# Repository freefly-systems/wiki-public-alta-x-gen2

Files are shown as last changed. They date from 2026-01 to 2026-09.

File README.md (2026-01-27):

# Alta X Gen2

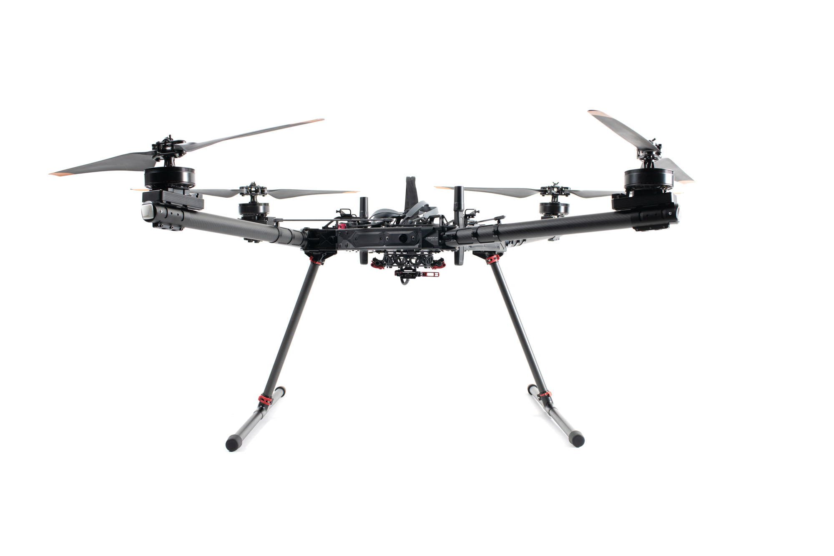
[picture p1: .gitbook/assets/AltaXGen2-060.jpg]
<figure><figcaption></figcaption></figure>

Alta X Gen2 is a professional multi-rotor aircraft designed for demanding cinematic, professional, and industrial applications. Building on the proven foundation of the original Alta X and incorporating advanced technologies from Astro, Gen2 delivers significant performance improvements alongside enhanced intelligence and capability. Alta X Gen2 continues the Freefly tradition of expandability and customization while bringing new innovations to the reliable workhorse platform that Alta pilots trust for their most critical missions.

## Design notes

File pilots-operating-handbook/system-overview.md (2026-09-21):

---
icon: book-open-lines
---

# System Overview

<figure><figcaption></figcaption></figure>

Alta X Gen2 is a professional multi-rotor aircraft designed for demanding cinematic, professional, and industrial applications. Building on the proven foundation of the original Alta X and incorporating advanced technologies from Astro, Gen2 delivers significant performance improvements alongside enhanced intelligence and capability. Alta X Gen2 continues the Freefly tradition of expandability and customization while bringing new innovations to the reliable workhorse platform that Alta pilots trust for their most critical missions.

## Key Components

### Alta X Gen2

Alta X Gen2 comes standard with 12mm rails and the Smart Dovetail isolator for quick payload swaps.

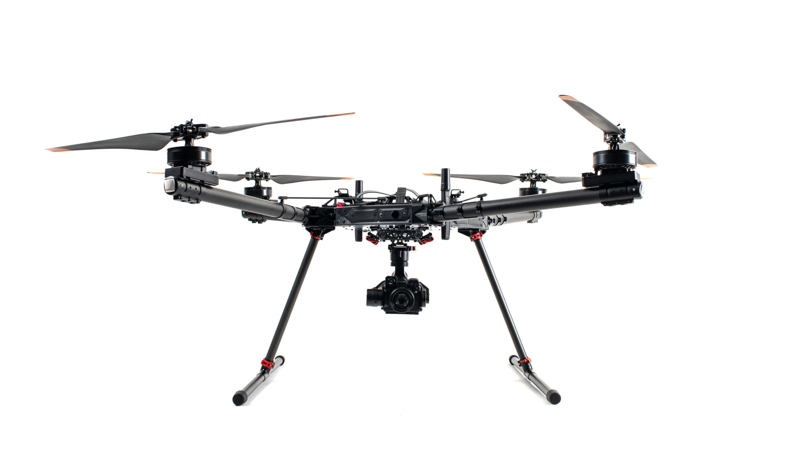
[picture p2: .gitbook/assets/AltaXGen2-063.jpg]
<figure><figcaption></figcaption></figure>

### Pilot Pro

Alta X Gen2 ships with [Pilot Pro](https://freeflysystems.com/pilot-pro), our custom controller, with either Herelink or Doodle radio. For more information, check the [Pilot Pro wiki](https://docs.freeflysystems.com/ecosystem/controller/pilot-pro/).

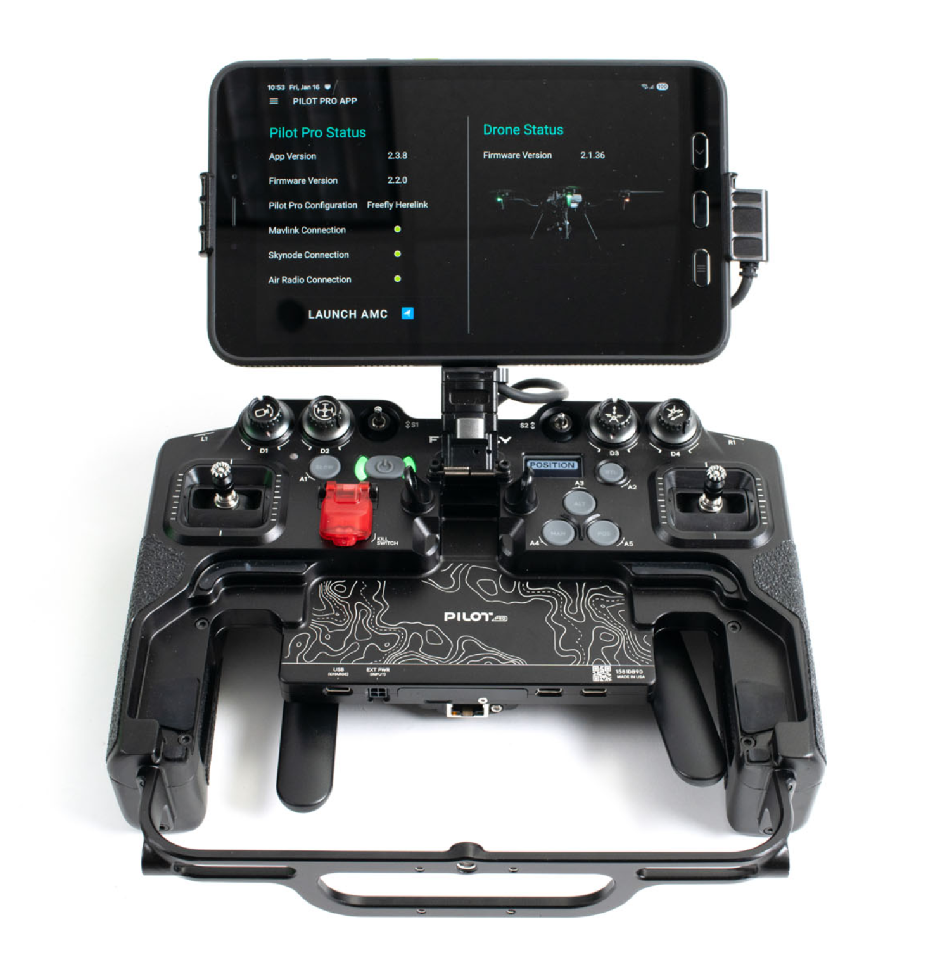
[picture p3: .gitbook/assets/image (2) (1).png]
<figure><figcaption></figcaption></figure>

### Batteries

Alta X Gen2 is designed to operate with two Tattu Plus 1.0 12S 16Ah smart batteries with AS150U connectors.

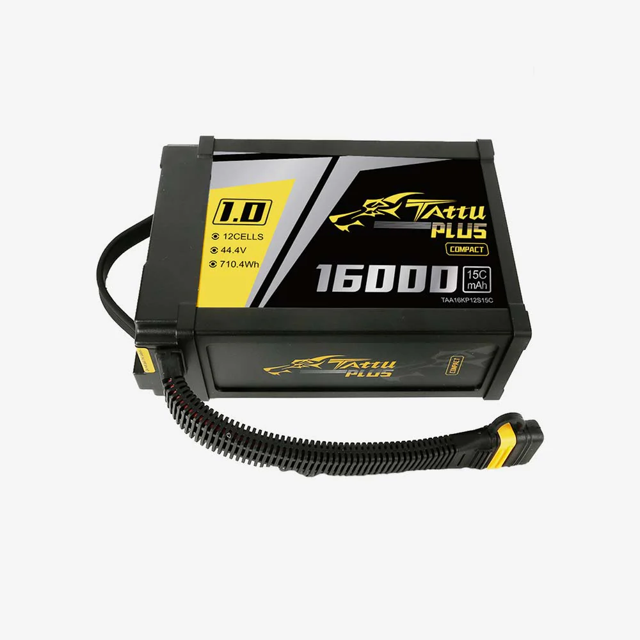
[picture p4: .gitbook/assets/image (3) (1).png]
<figure><figcaption></figcaption></figure>

### Charger

The Tattu TA3200 smart battery charger enables single connector charging for ease of use.

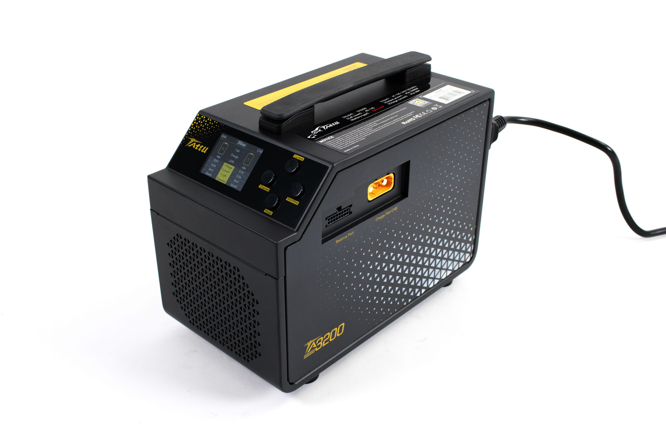
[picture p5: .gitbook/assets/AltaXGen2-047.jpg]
<figure><figcaption></figcaption></figure>

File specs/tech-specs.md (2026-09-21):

---
icon: bolt
---

# Tech Specs

## Propellers

| Material | Carbon Fiber Reinforced Nylon |
| --- | ---: |
| Propeller Orientation | (2x) CW and (2x) CCW Props |
| Propeller Type | Folding - 840 x 230 mm (33 x 9in) |

## Battery

| Cells | 12S |
| --- | ---: |
| Nominal Battery Voltage | 44.4V |
| Peak Battery Voltage | 50.4V |
| Battery Connectors | AS150U Anti Spark |
| Required Minimum Battery Discharge Rating (Per Pack) | 260A per battery (assumes two batteries) |

{% hint style="warning" %}
Battery hot swaps are not recommended. Please power off the aircraft by disconnecting both batteries when swapping packs to ensure ideal performance and battery lifespan.
{% endhint %}

{% hint style="info" %}
More information about the battery, button functions, and status LED indicator codes can be found in the [user manual](https://drive.google.com/file/d/1xZQplgB4Xa2VZYNrqxjLFh52dDPq8ldu/view)
{% endhint %}

Battery Tray Dimensions

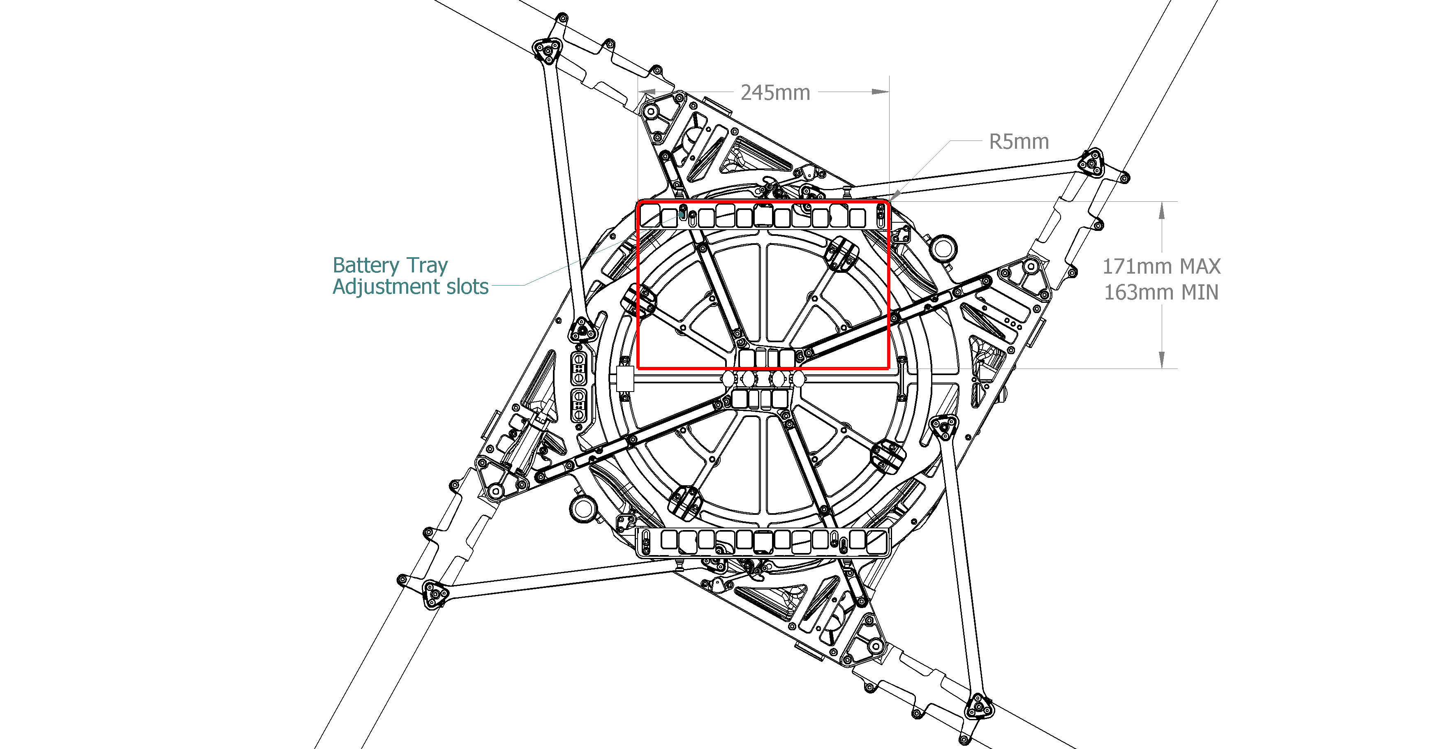
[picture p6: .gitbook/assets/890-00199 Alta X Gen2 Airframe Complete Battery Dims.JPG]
Minimum and Maximum Battery Tray footprint


Minimum Skyview Battery Tray Footprint

Maximum Skyview Battery Tray Footprint

Maximum Height of Battery for Skyview Mounting

## Weight 

| Maximum Gross Takeoff Weight | 34.9 kg |
| --- | --- |
| Maximum Payload | 15.1 kg |
| Empty Weight | 11.2 kg \* |

\*(0.13 kg heavier than Alta X Gen1 when similarly equipped with payload mounting rails, 12v & 24v regulators, and FPV camera)

## Environmental 

| Operating Temperature | -20C to +50C |
| --- | --- |
| Operating Ceiling | (Weight-dependent. See performance specs) |
| Ingress Protection | Tested to IP43 equivalent |

## Flight Controller

| Flight Controller Hardware | Freefly Custom Designed Skynode |
| --- | --- |
| Flight Controller Software | Auterion Enterprise PX4 (custom for Alta X) |
| Mission Control Software | Auterion Mission Control |
| Online Fleet Management | Auterion Suite |
| Flight Modes | Manual, Altitude Hold, Position Hold, Return, Autonomous Mission |
| Onboard Modules | Cortex-A53 Computer, LTE |
| Connectivity | Wifi, USB C, LTE (North America) |
| Supported Radios | Herelink and Doodle |
| Supported GNSS | L1/L2 bands for GPS, GLONASS, Beidou and Galileo |

## Radio Control

For more information on the Radio, please visit our [Pilot Pro Radio Specs](https://docs.freeflysystems.com/ecosystem/controller/pilot-pro/specs/radio-technical-specs)

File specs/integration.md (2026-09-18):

# Interfaces

Alta X Gen2 was designed to be easy to integrate custom payloads with a variety of electrical and communications interfaces.

### **USB-C** 

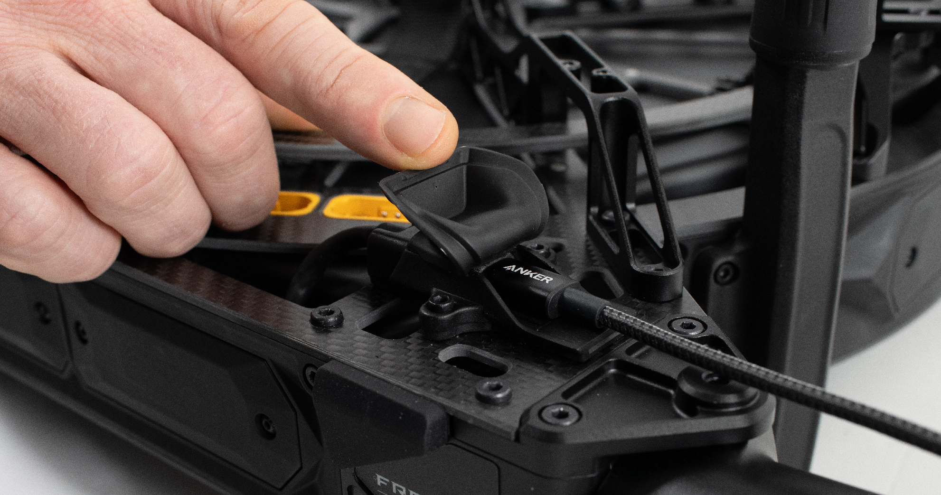
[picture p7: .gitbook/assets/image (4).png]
<figure><figcaption></figcaption></figure>

The USB-C connector is located on the top side chassis next to the battery connectors.&#x20;

By default it is configured as an ethernet adapter.

Functionality:

* connection to payload
* mass storage (e.g. flash drive)
* firmware updates

It is not possible to power Alta X Gen2 via this port.

### IO Panel

The IO panel is located in the forward bay door underneath the aircraft.

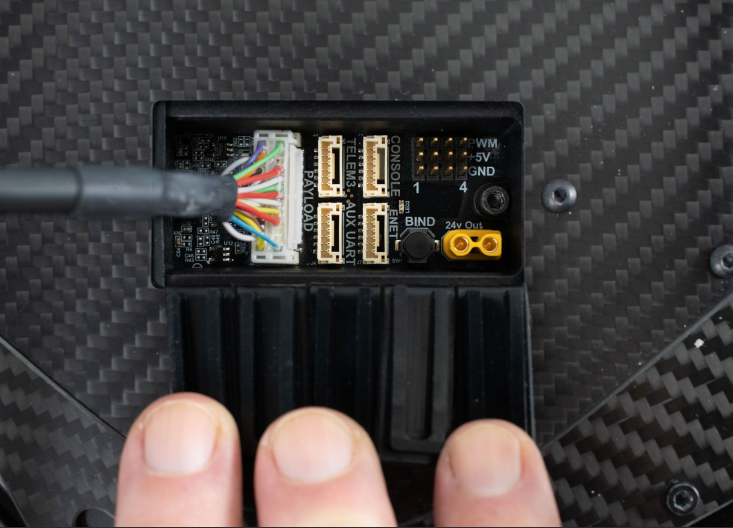
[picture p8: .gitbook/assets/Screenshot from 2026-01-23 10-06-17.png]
<figure><figcaption></figcaption></figure>

#### Payload 

Connector type: JST-ZPD 26-pin



This connector can be accessed directly or to pass connections to the [Smart Dovetail](https://docs.freeflysystems.com/astro/other-user-manuals/ecosystem/development-tools/payload-mounting-interfaces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) connector.

The mating connector to build a payload cable is [ZPDR-26V-S](https://www.digikey.com/en/products/detail/jst-sales-america-inc/ZPDR-26V-S/2472569).

PAYLOAD\_VBAT is 24V DC regulated, and is electronically fused at 6A. If the e-fuse trips, it will reset when the aircraft is power cycled. The e-fuse includes soft start protection for use with loads with high inrush current.&#x20;

#### TELEM3  

Connector: JST GH 6-pin



#### **AUX UART** 

Connector: JST GH 6-pin



#### **PWM** 

Connector: pin headers, 0.1 inch spacing



PWM outputs are active when the aircraft is powered on.

The PWM outputs on the Alta X Gen2 are controlled with the PWM\_AUX\_FUNC parameter where FUNC1-4 are the 4 PWM outputs. To assign a PWM output to a mapping, just find the number of the PWM output, and the associated PWM\_AUX\_FUNC and assign it to the desired mapping. ie, if you use RC AUX 1, it should use Dial 2 to control the PWM output.PWM output values (e.g. 1100 us) are controlled by these parameters (read more in the [PX4 Parameter Reference](https://docs.px4.io/main/en/advanced_config/parameter_reference#parameter-reference)).

| Parameter | Function |
| --- | --- |
| PWM\_AUX\_DIS1  | PWM output when autopilot is not armed. When set to -1 the value for PWM\_AUX\_DISARMED will be used. a similar parameter is available for each channel |
| PWM\_AUX\_MIN1  | Minimum PWM pulse for this output. When set to -1 the value for PWM\_AUX\_MIN will be used. |
| PWM\_AUX\_MAX1  | Maximum PWM pulse for this output. When set to -1 the value for PWM\_AUX\_MAX will be used. |
| PWM\_AUX\_REV1  | Invert direction. |
| PWM\_AUX\_FAIL1 | PWM output if autopilot is in failsafe mode. When set to -1 the value is set automatically depending if the actuator is a motor (900us) or a servo (1500us) |

#### Ethernet

Connector: JST GH 6-pin

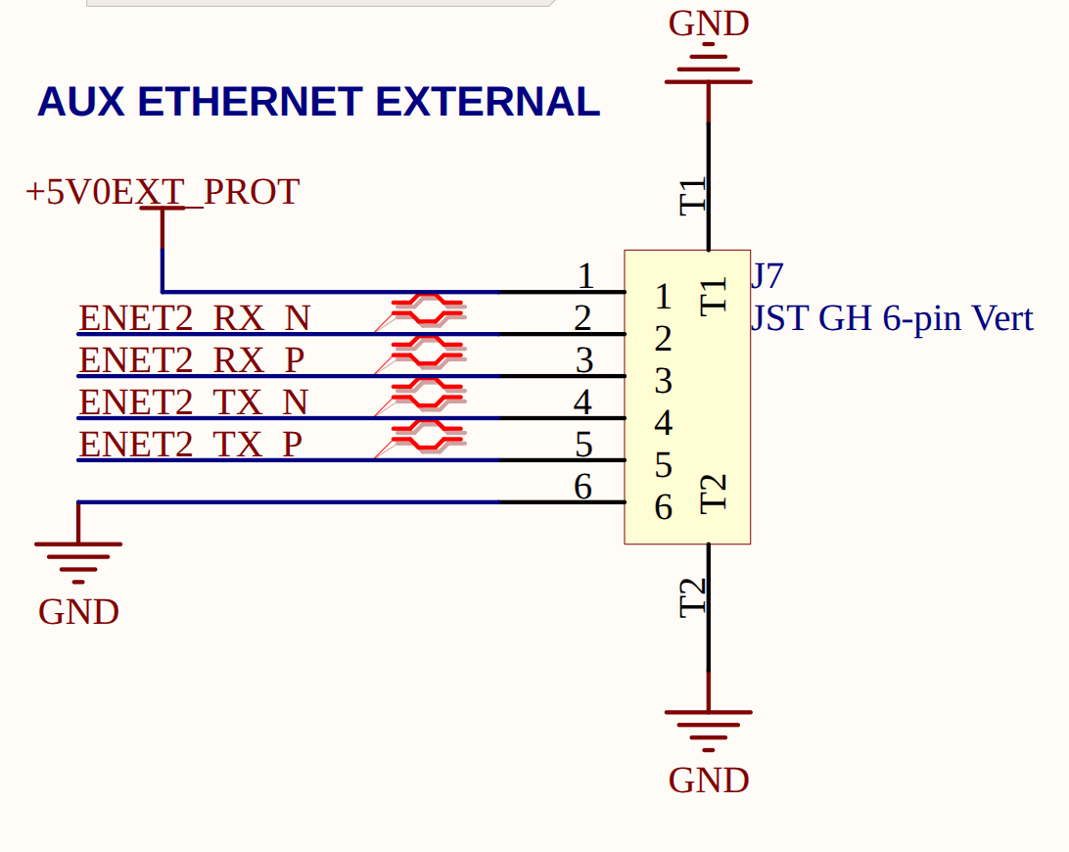
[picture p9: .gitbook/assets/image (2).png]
<figure><figcaption></figcaption></figure>

This Ethernet port is connected to the Ethernet switch on the IO panel and connects to the payload and Skynode.

A secondary RJ45 jack is also available inside the tub on the IO panel PCBA. This is connected to the same Ethernet switch as the ENET GH connector.&#x20;

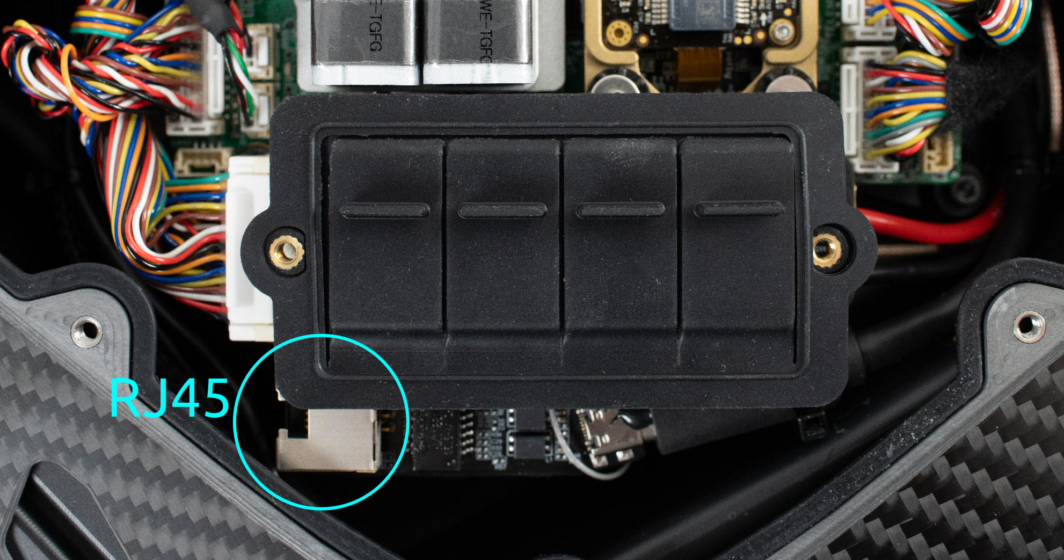
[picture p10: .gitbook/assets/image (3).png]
<figure><figcaption></figcaption></figure>

#### XT30 Power

The XT30 connector supplies regulated 24V DC power. It's electronically fused at 6A. If tripped, it will reset when the aircraft is power cycled.  This 24V source is shared with the other 24V connection points on the aircraft. The e-fuse includes soft start protection for use with loads with high inrush current.&#x20;

### External Power Connectors

In the rear bay of the aircraft, there are external facing power connectors.&#x20;

Both of these are regulated from the battery voltage.&#x20;

* 12V is available up to 120W or 10A.&#x20;
* 24V is available up to 240W or 10A.&#x20;

### Rear Power Connections

Alta X Gen2 provides power connections inside and outside the aircraft tub. This is useful for integrations that sit in the payload bay, or for devices that are attached outside of the tub.&#x20;

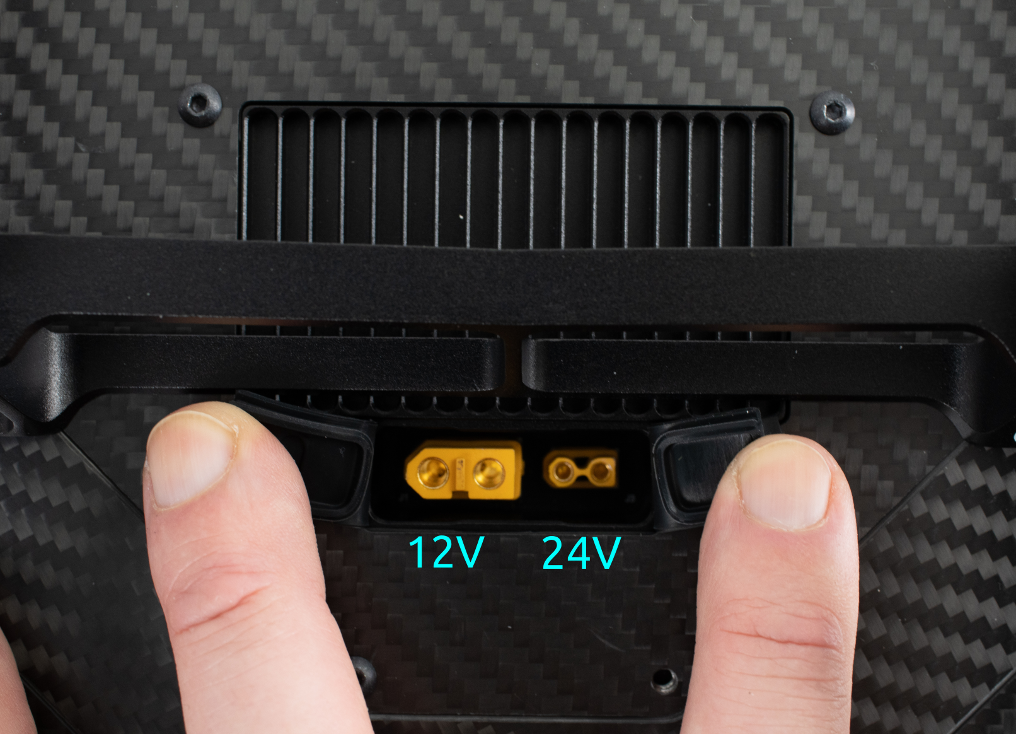
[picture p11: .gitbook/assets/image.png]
<figure><figcaption></figcaption></figure>

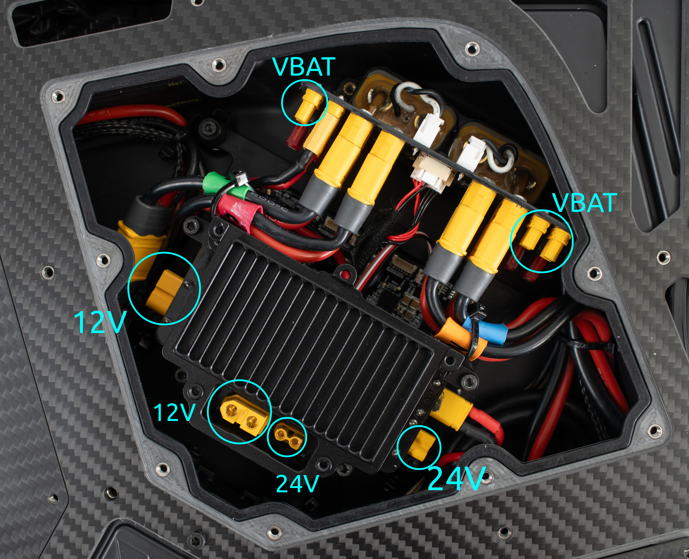
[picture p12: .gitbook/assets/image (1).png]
<figure><figcaption></figcaption></figure>

#### 12V power

12V power is available on XT60 connectors, one internal and one external.&#x20;

Max current draw is 10A/120W

#### 24V power

24V power is available on the XT30 connectors on the DC-DC regulator, one internal and one external. This source is shared with the payload ZPD connector and the IO panel XT30 connector.

Max current draw is 10A/240W

{% hint style="warning" %}
VBAT (\~44V) is also available on an XT30 connector, always double check the voltage on the connector before plugging something in.
{% endhint %}

{% hint style="warning" %}
Keep in mind, when drawing power from the 12V or 24V regulators on the ground, the heatsink may become warm to the touch. Once in flight, airflow around the aircraft helps keep it cool.
{% endhint %}

#### VBAT power

The battery breakout board includes 4x XT30 connectors fused at 10A each. One of these feeds the 12/24V DC-DC regulator, but the remaining connectors are available for use.&#x20;

These are electrically connected directly to the battery bus, nominally 44.4V (12S LiPo).

### Onboard Network Connectivity

The Ethernet switch on Alta X Gen2 provides connectivity to attach payloads or custom devices to the aircraft's onboard network. Any device on the switch can access any other devices connected to the switch, including the Skynode and Payload.&#x20;

The internal network is setup with the subnet 192.168.144.0/24, with subnet mask 255.255.255.0.&#x20;

IP addresses are statically allocated. The reserved addresses include:

| IP | Endpoint |
| --- | --- |
| 192.168.144.10 | Airside Radio |
| 192.168.144.11 | Pilot Pro |
| 192.168.144.12 | Ground Radio  |
| 192.168.144.20 | Skynode |

Ethernet based payloads generally have reserved IP addresses that vary per payload.

To connect a custom device, we recommend using an IP address in the range of

&#x20;`192.168.144.200` -  `192.168.144.255`.

{% hint style="info" %}
The radio link to the ground has limited bandwidth, and the internal network is 10/100mb Ethernet. Be mindful of the bandwidth needs of custom devices when connecting them to the aircraft to not overload the network.
{% endhint %}

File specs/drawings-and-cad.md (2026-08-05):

---
icon: unity
---

# Drawings & CAD

### Aircraft Dimensions

| Dimension | Length \[mm] |
| --- | --- |
| Unfolded Diameter (not including props) | 1570 |
| Unfolded Diameter (Including Props) | 2273 |
| Folded Diameter | 877 |
| Height with landing gear (medium legs, ground to top of prop mount) | 694 |
| <p>Height from chassis underside to ground</p><p>(medium leg length landing gear, included)</p> | 450 |
| <p>Height from chassis underside to ground</p><p>(long leg length landing gear)</p> | 580 |

### Mounting Interfaces - Chassis Underside

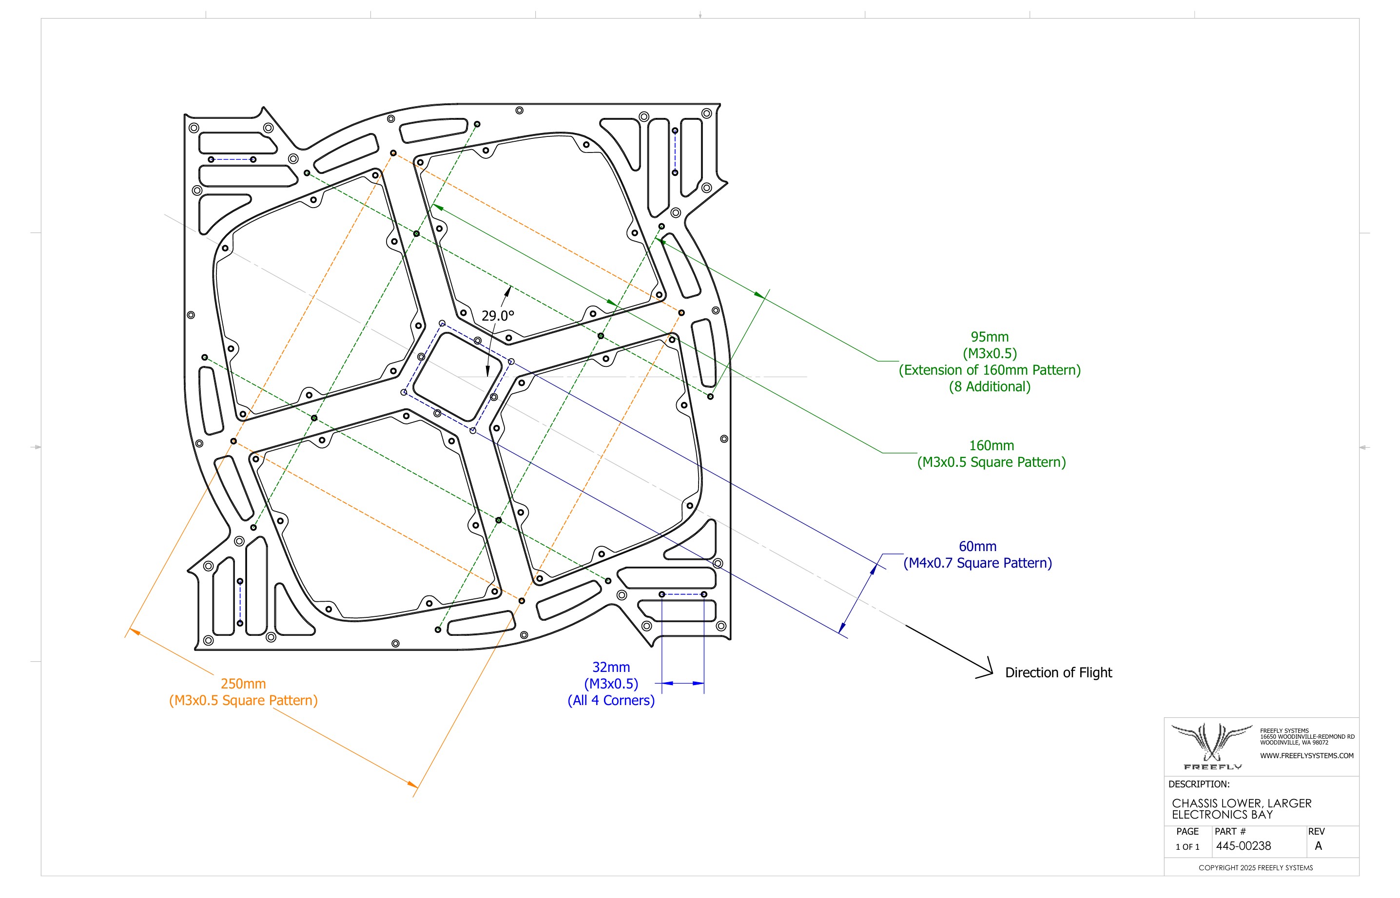
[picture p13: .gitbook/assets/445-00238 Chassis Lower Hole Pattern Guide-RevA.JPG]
<figure><figcaption></figcaption></figure>

{% file src="../.gitbook/assets/445-00238 Chassis Lower Hole Pattern Guide-RevA.pdf" %}

### Mounting Interfaces - Chassis Top

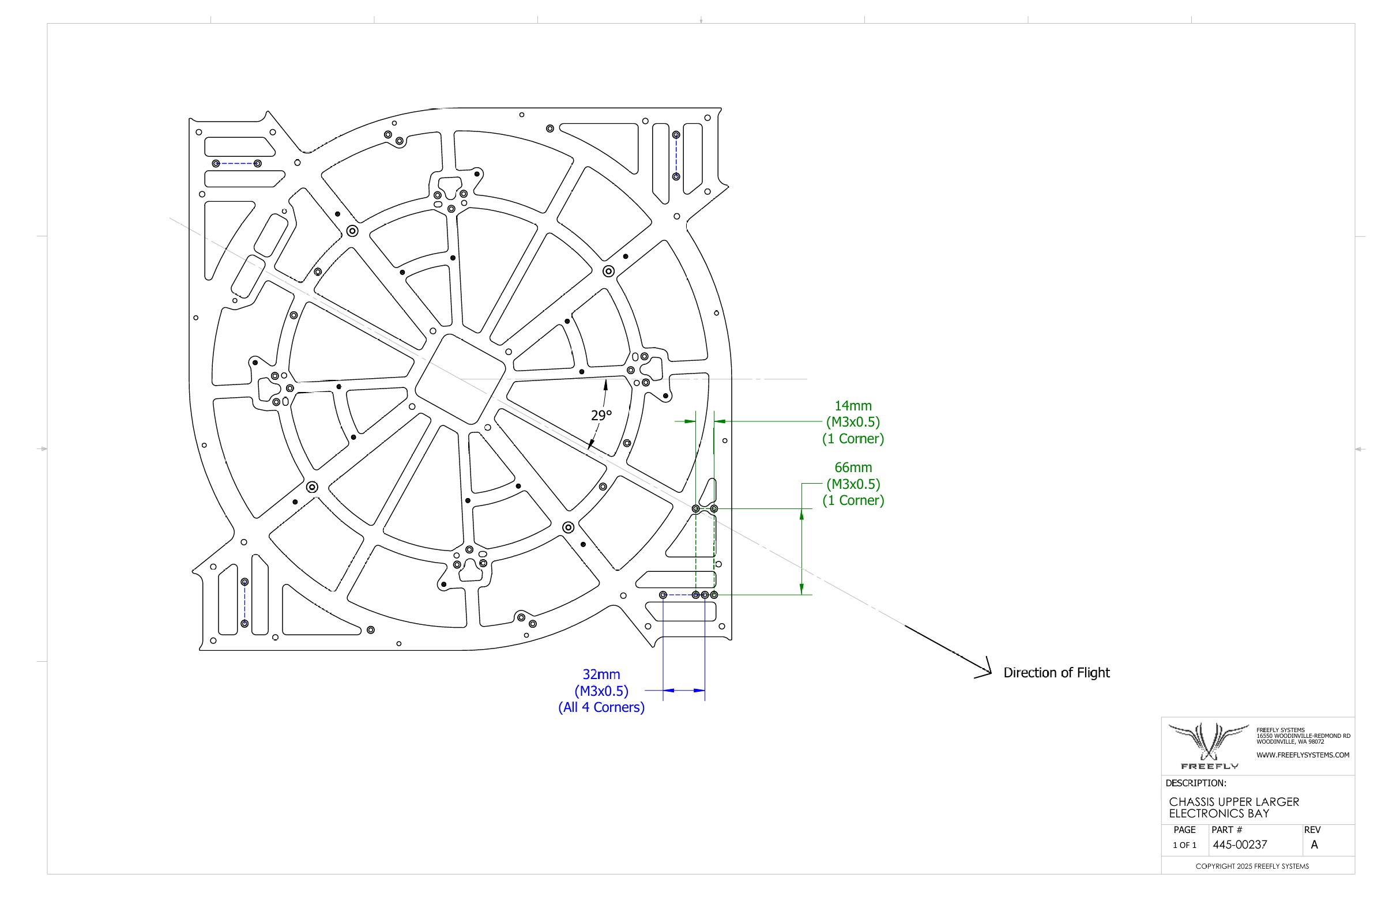
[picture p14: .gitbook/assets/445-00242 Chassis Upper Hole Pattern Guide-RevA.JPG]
<figure><figcaption></figcaption></figure>

{% file src="../.gitbook/assets/445-00242 Chassis Upper Hole Pattern Guide-RevA.pdf" %}

### Electronics Bay Door

Electronics bay access panel. Start with this model and customize as needed.

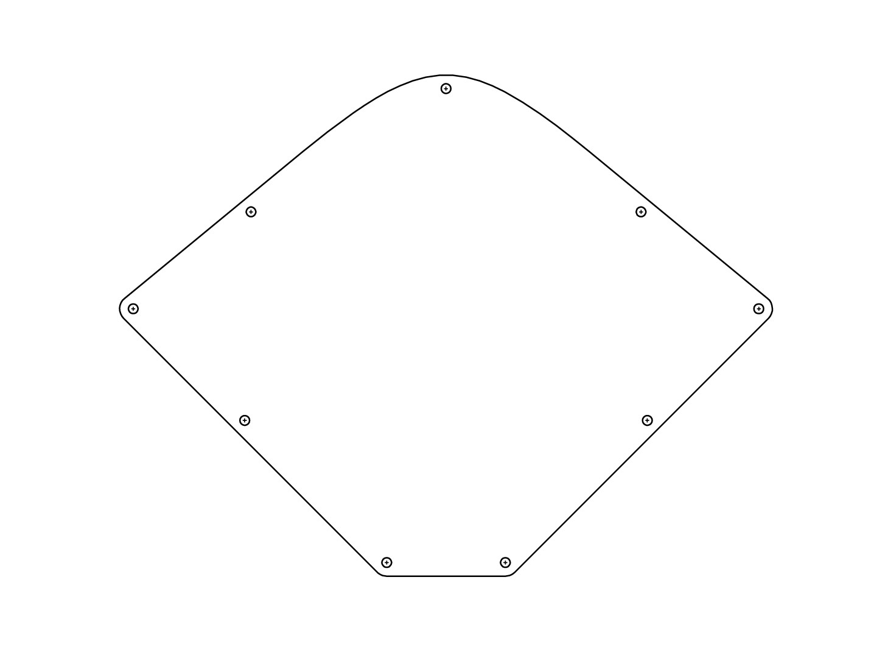
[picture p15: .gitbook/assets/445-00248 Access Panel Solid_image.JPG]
<figure><figcaption></figcaption></figure>

{% file src="../.gitbook/assets/445-00248 Access Panel Solid-RevA.DXF" %}

{% file src="../.gitbook/assets/445-00248 Access Panel Solid-RevA.step" %}

### Electronics Bay Mount Interface

Location of four mounting posts in electronics bay and a sample part.

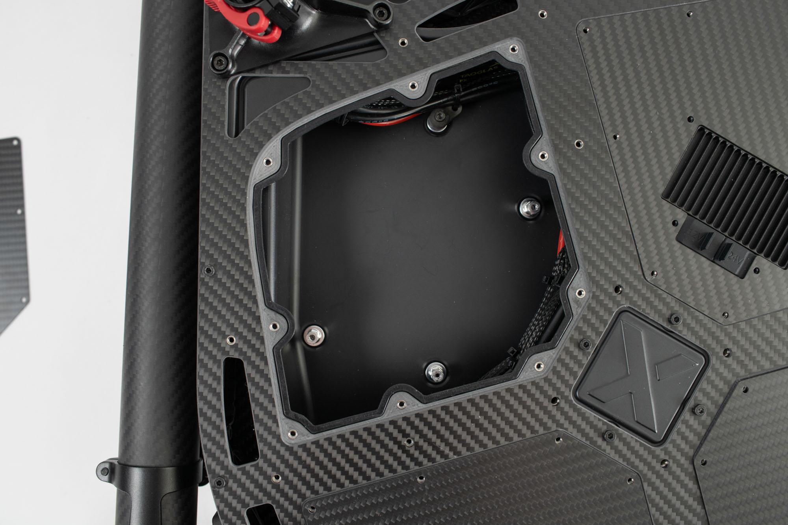
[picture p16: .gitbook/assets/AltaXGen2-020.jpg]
<figure><figcaption></figcaption></figure>

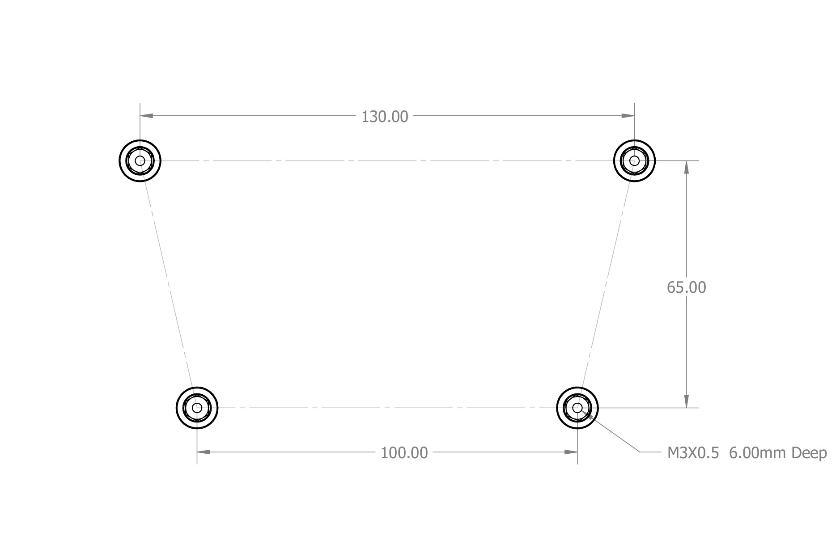
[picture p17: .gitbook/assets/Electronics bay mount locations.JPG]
<figure><figcaption></figcaption></figure>

{% file src="../.gitbook/assets/430-00494 Mount Compute-Rev01.step" %}

### Chassis CAD Files

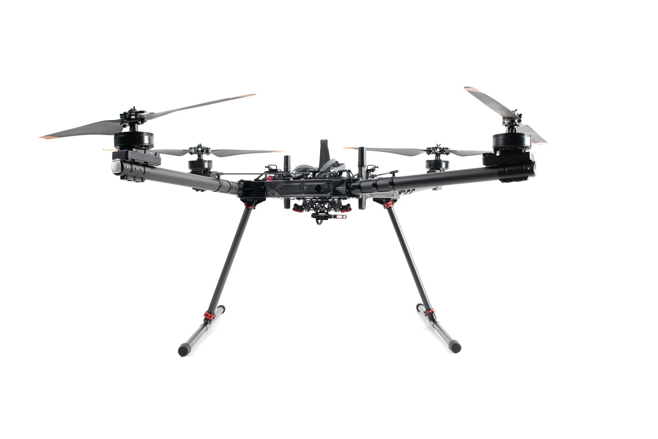
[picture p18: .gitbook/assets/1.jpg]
<figure><figcaption></figcaption></figure>

Parasolid format is recommended.

[Alta X Gen2 Chassis STEP](https://drive.google.com/file/d/1a5O9uxuC2gIbU3ASWuEZi3WIqzA3-_oC/view?usp=drive_link) / [Alta X Gen2 Chassis Parasolid](https://drive.google.com/file/d/1hoIQWwE8XIOoxELjjjahPo31PFKZMx0d/view?usp=drive_link)

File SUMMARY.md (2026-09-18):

# Table of contents

* [Alta X Gen2](README.md)

## Pilot's Operating Handbook

* [Getting Started](pilots-operating-handbook/getting-started.md)
* [System Overview](pilots-operating-handbook/system-overview.md)
* [Flight Part 1 - Modes](pilots-operating-handbook/flight-modes.md)
* [Flight Part 2 - Operation](pilots-operating-handbook/operation.md)
* [Flight Part 3 - Emergency Procedures](pilots-operating-handbook/emergency-procedures.md)
* [Pro-tips and Limitations](pilots-operating-handbook/pro-tips-and-limitations.md)
* [Ecosystem / Payloads / Accessories / Workflows](pilots-operating-handbook/ecosystem-payloads-accessories-workflows.md)

## Maintenance

* [Standard Maintenance Procedures](maintenance/standard-maintenance-procedures.md)
* [Network and Connectivity](maintenance/network-and-connectivity.md)
* [Software Updates](maintenance/software-updates/README.md)
  * [Updating Firmware](maintenance/software-updates/updating-firmware.md)
* [FAQ & Troubleshooting](maintenance/troubleshooting.md)

## Specs

* [Tech Specs](specs/tech-specs.md)
* [Performance Data](specs/performance-data.md)
* [Drawings & CAD](specs/drawings-and-cad.md)
* [Interfaces](specs/integration.md)

## Other user manuals

* [Ecosystem](other-user-manuals/ecosystem/README.md)
  * [Rails and Isolator](other-user-manuals/ecosystem/rails-and-isolator.md)
  * [Batteries and Charging](other-user-manuals/ecosystem/batteries-and-charging.md)
* [Compliance](other-user-manuals/compliance.md)
* [Legal](other-user-manuals/legal.md)

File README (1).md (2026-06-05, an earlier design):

---
description: How to get set up for a successful and safe first flight!
---

# Getting Started

<figure><figcaption></figcaption></figure>

## 1. Unboxing and Assembly

a. Remove the landing gear components from the top lid of the case.

b. Insert leg tubes into T-joints until seated, lock red clamps. _(The leg tubes and skids are interchangeable.)_

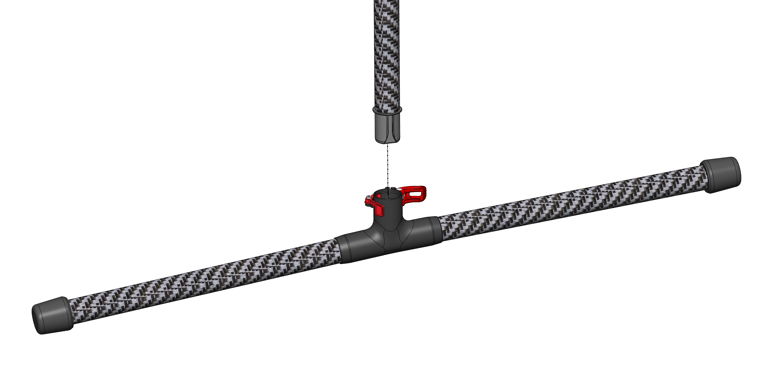
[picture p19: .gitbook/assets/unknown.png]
<figure><figcaption></figcaption></figure>

c. Place Alta X Gen2 upside down, open locking levers, insert landing gear into leg mounts. Ensure both levers and safety latches are fully engaged.

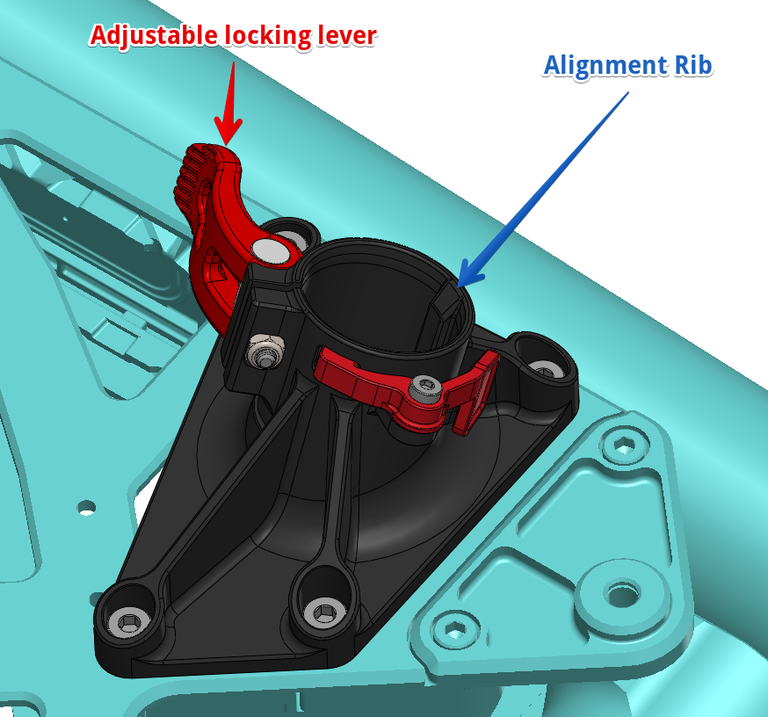
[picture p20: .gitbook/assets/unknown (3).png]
<figure><figcaption></figcaption></figure>

d. Flip aircraft onto landing gear.

e. If using a payload, connect it to the Smart Dovetail while aircraft is powered off. _(Payloads are not hot swappable)_

## 2. Power On

a. Power on Pilot Pro. Wait for the tablet to boot up.

b. For ground operation: Connect one battery using the fused cable to either battery connector on Alta X Gen2.

c. For flight: Connect two batteries directly (no fused cable).

{% hint style="warning" %}
**Safety Note:** Always use the fused cable with a single battery when not flying. This prevents accidental arming. Never connect a second battery through the fused cable.
{% endhint %}

d. Wait for the LED on the Pilot Pro's power button to turn green. Then open the AMC app.

## 3. Connect to WiFi and Auterion Suite (Optional)

_Enables automatic log uploads, online fleet and asset management, and direct log sharing with Freefly support—the fastest way to get help if issues arise._

a. With Alta X Gen2 powered on, open AMC and navigate to Vehicle Overview > Connectivity.

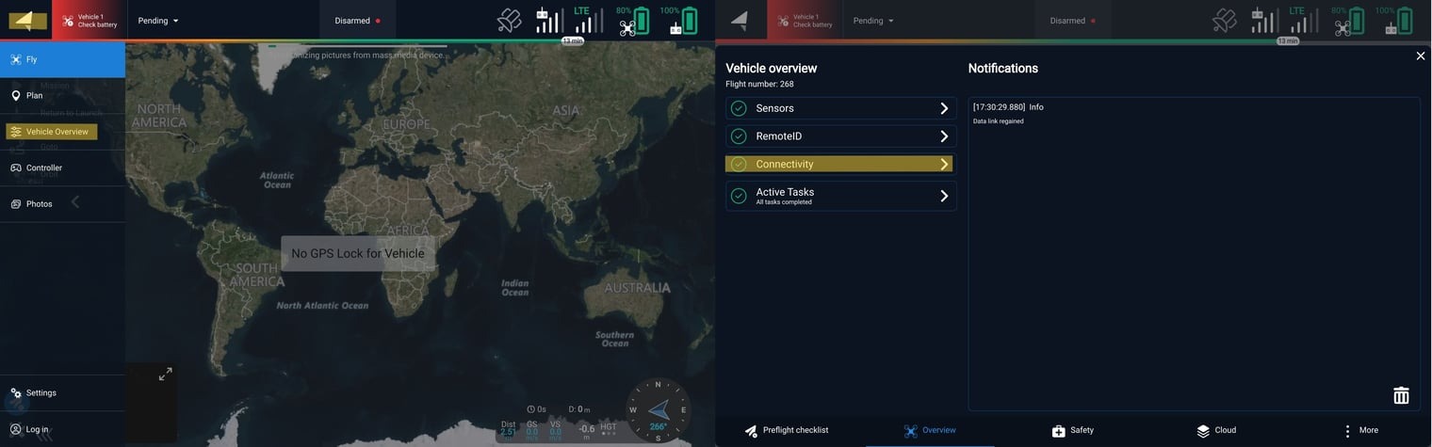
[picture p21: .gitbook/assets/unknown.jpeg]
<figure><figcaption></figcaption></figure>

b. Enable WiFi (not hotspot mode), enter network credentials, and click Connect.

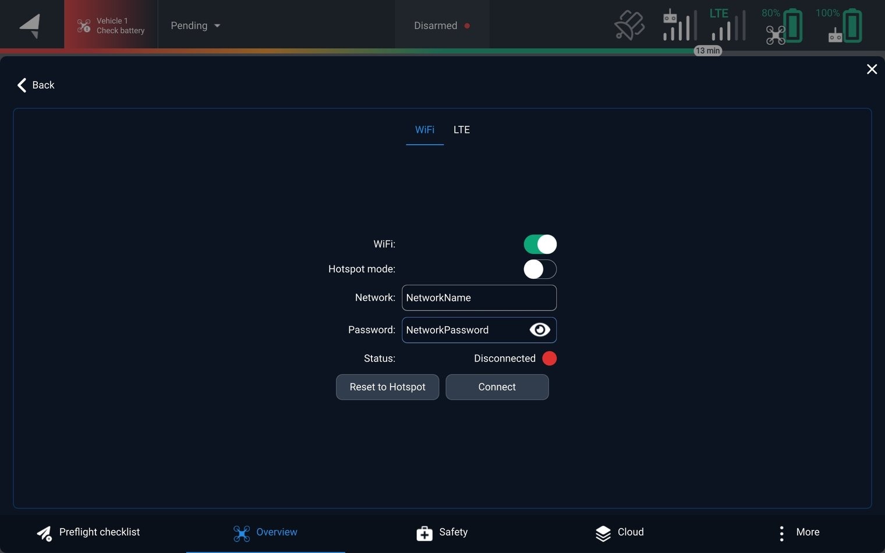
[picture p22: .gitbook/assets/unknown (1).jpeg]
<figure><figcaption></figcaption></figure>

c. Connect USB-C cable from computer to Alta X Gen2 (port located near battery connectors).

d. Navigate to http://10.41.1.1 in a web browser.

e. Follow prompts to create account or add aircraft to existing fleet.

f. Once the registration is complete, navigate to http://10.41.1.1. Enable Cloud Services and Flight Log Upload in Settings.

## 4. Charge and Update

You should have received an Alta X Gen2 in a case and a separate shipment of Alta X Gen2 batteries and chargers (We have to ship separately due to Dangerous Goods shipping requirements.)

a. Charge aircraft batteries using a Tattu Smart Charger. _(Balance leads are not required for charging the Gen2 Smart Batteries)._

b. Charge Pilot Pro with the included 45W USB-C charger.

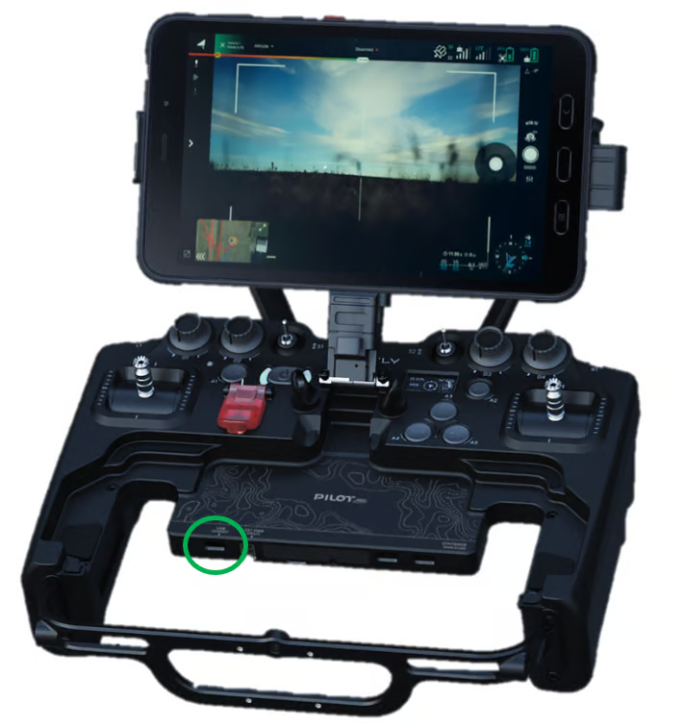
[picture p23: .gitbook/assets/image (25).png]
<figure><figcaption></figcaption></figure>

c. Verify firmware is current on both aircraft and controller.

## 5. Go Flying

a. While the batteries and controller are charging, read the [PILOT'S OPERATING HANDBOOK](https://app.gitbook.com/s/mvvtTxCd0o4luBB04PQp/pilots-operating-handbook "mention").

***

This Aircraft Flight Manual describes the complete operation of airframe and flight control systems, and the normal maintenance of those items. Do not operate Alta X Gen2 without reading and understanding this manual.

‌This manual is not a substitute for adequate flight training. Training requirements can vary when operating in different countries or under different flight conditions. Always consult local regulations before flying Alta X. In areas where there are no flight training requirements, it is the sole determination of the pilot-in-command as to whether he or she has the appropriate level of training or experience for a given flight. Always set and adhere to personal minimums and fly within your own capabilities.

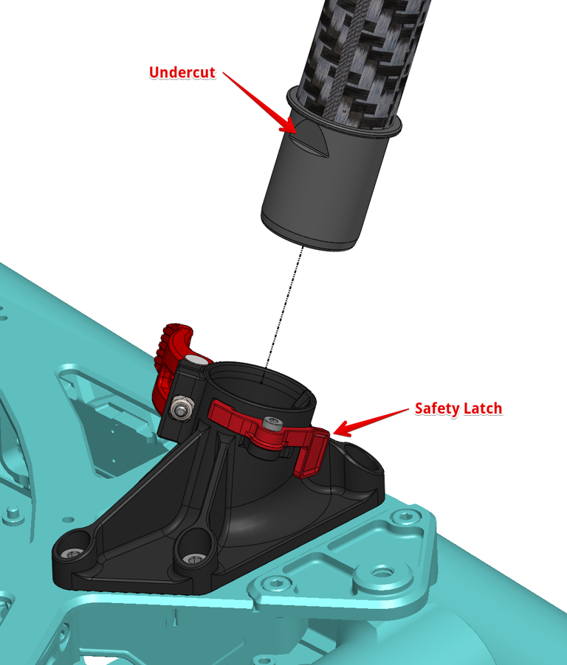
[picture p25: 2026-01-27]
.gitbook/assets/unknown (10).png

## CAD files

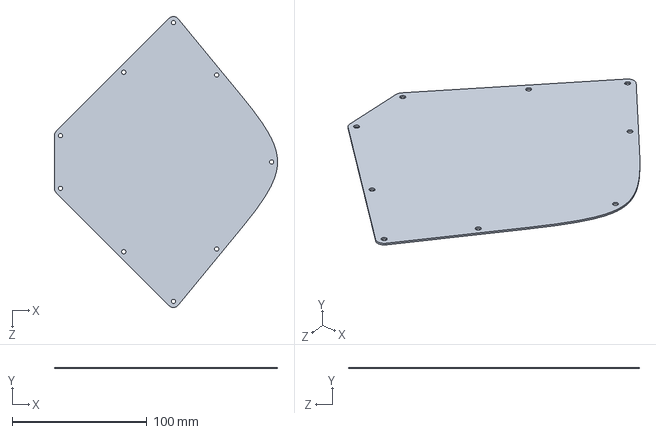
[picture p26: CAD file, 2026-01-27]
.gitbook/assets/445-00248 Access Panel Solid-RevA.step
165.8 x 1.00 x 216.2 mm

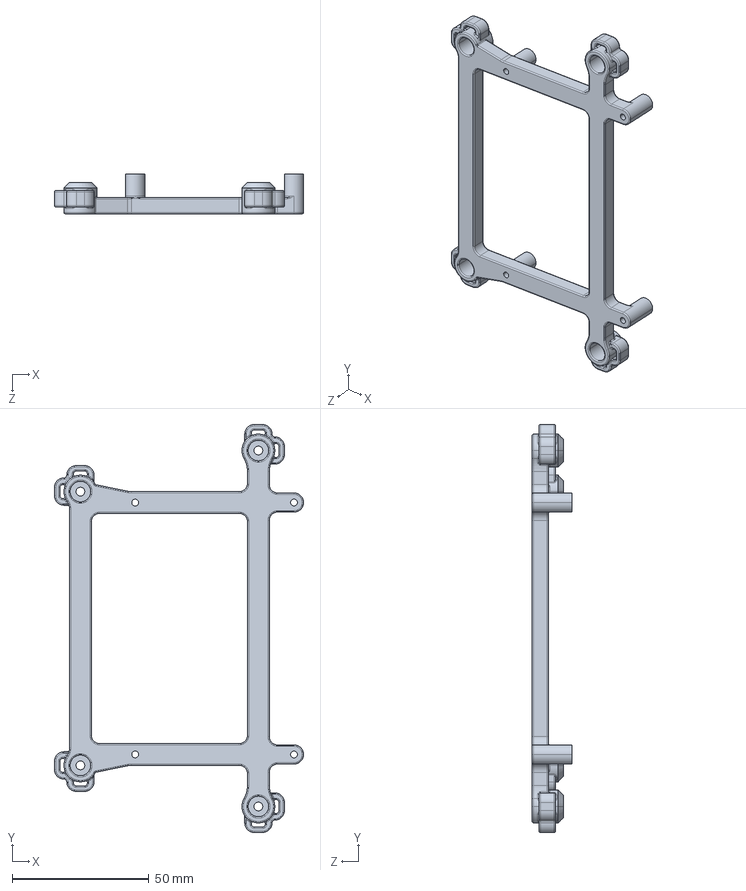
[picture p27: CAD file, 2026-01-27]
.gitbook/assets/430-00494 Mount Compute-Rev01.step
91.0 x 149.0 x 14.5 mm

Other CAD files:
.gitbook/assets/445-00248 Access Panel Solid-RevA.DXF

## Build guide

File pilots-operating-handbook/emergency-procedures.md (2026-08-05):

---
icon: drone-front
---

# Flight Part 3 - Emergency Procedures

## General Guidance

**Human safety must be the top priority. Aircraft can be replaced. People cannot. Always prioritize the safety of yourself and others over the preservation of aircraft or equipment.**

Emergency situations are dynamic events, that will not often conform perfectly to the categories listed below. A thorough understanding of aircraft systems, proficiency in piloting the aircraft, and sound judgment will allow you to bring about the best possible outcome in an emergency.

The likelihood of an emergency can be reduced substantially through proper aircraft maintenance, the use of [checklists for normal procedures](operation.md#flight-checklists), and careful pre-flight planning. The likelihood of a safe flight often depends on the diligence of the pilot, both before taking off and during operation.

In general, if an emergency occurs, three basic actions can be applied to most situations:

1. Maintain aircraft control — Small emergencies can quickly escalate if the pilot is distracted attempting to troubleshoot the problem. Always maintain visual contact with the aircraft during an emergency to reduce the likelihood of losing orientation.
2. Analyze the situation — Once the aircraft is stabilized, assess the cause of the emergency.
3. Take appropriate action — In many cases, the appropriate action will be to land the aircraft as soon as possible. Aircraft can be replaced.

### Return Mode

Do not be over-reliant on [Return Mode](emergency-procedures.md#return-mode) in emergencies. The cause of the emergency may degrade or disable Return Mode (e.g., GPS loss disables Return Mode).

By default, stick movements do not interrupt Return Mode. Press a flight mode button to exit Return Mode.

***

## Emergency Checklists

The flight [checklists](operation.md#flight-checklists) contain concise instructions to follow to mitigate risk in the event of an in-flight emergency. Some of these situations are discussed in more detail below.

{% tabs %}
{% tab title="Orientation Loss" %}
#### Loss of Orientation

If orientation is lost, neutralize inputs and activate position mode. Then work to identify the front of the aircraft.

We recommend identifying the front of the aircraft via a "guess and check" method of small roll right inputs alternating with yawing the aircraft 90 degrees at a time. We recommend a roll input rather than pitch because at a distance it is easier to see lateral motion than fore/aft motion.

If it is not possible to identify orientation, and it is safe to activate Return Mode, do so. By default in Return Mode, after climbing, the aircraft will yaw to put the front toward the direction of flight.

Resume flying or land as necessary.
{% endtab %}

{% tab title="Unexpected Behavior" %}
#### Unexpected Aircraft Behavior

If aircraft behaves unexpectedly, do the following: neutralize inputs, activate Position Mode, and observe the aircraft. If it is still flying in an uncommanded manner in Position or Altitude Mode, switch to Manual Mode.

In some cases, unexpected behavior is due to degraded GPS signal or erroneous sensor readings (e.g. compass error). In such cases, Return Mode may not behave reliably. Manual Mode does not rely on these sensors.

Land as soon as possible.
{% endtab %}

{% tab title="Landing Detector Failure" %}
#### Landing Detector Failure

If the aircraft touches down, but hops back up into the air several times, or sits on the ground with the props continuing to spin, the autopilot may not have detected a landing. Climb and retry landing with a greater downward velocity.

{% hint style="info" %}
Landing the aircraft firmly will give the accelerometers and gyroscopes a sufficient contrast between flight and landing.
{% endhint %}

If an attempted landing is unsuccessful in Position and Altitude mode, land in Manual Mode.

If an attempted landing is unsuccessful in Manual Mode, perform an Emergency Stop (see below) with the aircraft on the ground or as close as possible.
{% endtab %}

{% tab title="GPS Loss" %}
#### Loss of GPS

If GPS is lost, flight modes that rely on GPS (Position, Return, Mission, etc) will not be available. If the aircraft is in Position mode when GPS is lost, the autopilot will switch to Altitude Mode. If the aircraft is in Return or Mission modes when GPS is lost, it will automatically start landing. Landing can be overridden by the pilot by changing modes to Altitude or Manual modes.

{% hint style="info" %}
It is the pilot's responsibility to be proficient with Altitude and Manual Mode and to have the aircraft configured to behave safely if GPS is lost.
{% endhint %}

Examples of behavior without GPS:

* If GPS is not available upon arming, no Home Point is set, and Return Mode is not available. Even if GPS becomes available while flying, Return Mode will not be available.
* If the pilot commands Return Mode, the aircraft will remain in Altitude or Manual Mode, and an error will be displayed on the pilot handset.
* If Land Mode is activated (e.g. by a failsafe), the aircraft will descend as though in Altitude mode, maintaining a consistent descent but drifting with the wind.
* If GPS is lost in Position, the aircraft will display a warning and switch flight mode to either Altitude Mode or Manual Mode, depending on the degradation of the signal and other sensors
* If GPS is providing altitude information (e.g. while using RTK GPS), and GPS is lost, the ability of Altitude Mode to accurately maintain altitude may be affected.
{% endtab %}

{% tab title="RC Loss of Signal (LOS)" %}
#### RC Loss of Signal (LOS)

RC Loss of Signal (LOS) can occur if the pilot handset signal is degraded or stops, or if aircraft does not receive the signal due to distance or interference (e.g. from obstacles or other radio signals).

If the signal is lost longer than the RC Timeout, a failsafe action will be triggered. The RC Timeout is quite short by default: 0.5 seconds. The pilot may not have time to react before the failsafe action is activated. By default, the failsafe action is Return Mode.

If the signal is lost, check the pilot's handset power and [antenna orientation](pro-tips-and-limitations.md#antenna-positioning). Antenna orientation is especially important when Astro is far from the pilot.

If the signal is recovered, the pilot will be able to take control by pressing a flight mode button.
{% endtab %}

{% tab title="Video Loss" %}
#### Loss of Video Signal

Loss of Video Signal can occur if the aircraft flies out of range or if it flies behind an object that interrupts the signal. Maintaining visual contact is the preferred method to re-establish control of the aircraft, either with the pilot seeing the aircraft or by the use of a visual observer.

Yawing the aircraft can help signal reception if the body of the aircraft is blocking the line of sight between the transmitter and receiver antennas.

If video signal or visual contact cannot be re-established, enable Return Mode to bring the aircraft back to signal reception range.

{% hint style="danger" %}
It is the responsibility of the pilot to see and avoid other aircraft, people, or obstacles. Always maintain a direct line of sight with Astro during flight, use visual observers as operations require, and follow local regulations regarding see-and-avoid requirements.
{% endhint %}
{% endtab %}
{% endtabs %}

***

## Emergency Stop

{% hint style="danger" %}
**As a last resort, if it is not possible to land or control the aircraft, perform an Emergency Stop. If performed while flying, this will cause the aircraft to crash. Perform the Emergency Stop as far away from people as possible.**
{% endhint %}

There are three ways to initiate emergency stop:

* Pilot Pro: Flip open the red Kill Switch cover and pull the Kill Switch down
* Pilot Pro: In Manual Mode, hold the throttle stick down and left for 10 seconds.
* AMC: Tap "Armed" button (top center of screen) and swipe/hold to shut down. This will work even when the aircraft is airborne.

***

## Failsafes

Failsafe behavior and settings are configured in AMC. The [AMC documentation ](https://docs.auterion.com/vehicle-operation/settings-and-maintenance/safety)covers each failsafe and related settings in detail.

{% hint style="warning" %}
We strongly recommend using the default settings, changing only Return Altitude, unless you are an expert user and have tested the effect of changes thoroughly.
{% endhint %}

#### Low Battery Failsafe

As the battery level becomes low, the autopilot can take action. The default settings do not interfere until the battery becomes quite low. Additionally, low battery failsafes are only able to estimate how long it will take the aircraft to return to the home point. This means it is the pilot's responsibility to be aware of the battery level and ensure the aircraft is on the ground.

Autopilot uses a variety of inputs to warn or take action.

* State of Charge (SoC) of the batteries.
* Onboard voltage measurement.
* Complex time to home estimation based on flight characteristics

| State | Triggered By | Action |
| --- | --- | --- |
| Warning | 30% SoC | Warning only |
| Critical  | 20% SoC | Return Mode  |
| Critical  | Distance to home estimation | Return Mode  |
| Emergency | 10% SoC | Warning only |
| Emergency | 43.5 Volts | Warning only |

{% hint style="info" %}
When activated by a low battery failsafe, Return and Land Mode cannot be overridden by stick movement. They can be overridden by pressing a flight mode button (e.g. Position).
{% endhint %}

***

## Error and Warning Indication

The aircraft communicates the presence of errors and warnings primarily through Auterion Mission Control (AMC) [status indicators](https://docs.auterion.com/auterion-mission-control/fly/fly-view-ui-overview#vehicle-status-indicators-top-bar) on the pilot handset or PC. Many messages are accompanied by an audible message (e.g. "Return Flight Mode"). Additionally, Alta X Gen2 boom LEDs will flash when the battery level is critical.

Status messages, including errors and warnings, are stored in Flight Logs. After any emergency, review the log to determine the source of the problem.

If the meaning of an error or warning is not clear, please [contact Freefly Support](https://freeflysystems.com/contact). Share as much detail as possible, including sharing the flight log.

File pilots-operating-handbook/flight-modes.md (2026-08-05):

---
description: Understand the Flight Modes available on Alta X Gen2
icon: drone-front
---

# Flight Part 1 - Modes

Alta X Gen2 offers several flight modes with varying levels of pilot assistance.

Flight mode can be changed via the buttons on Pilot Pro or the AMC app.

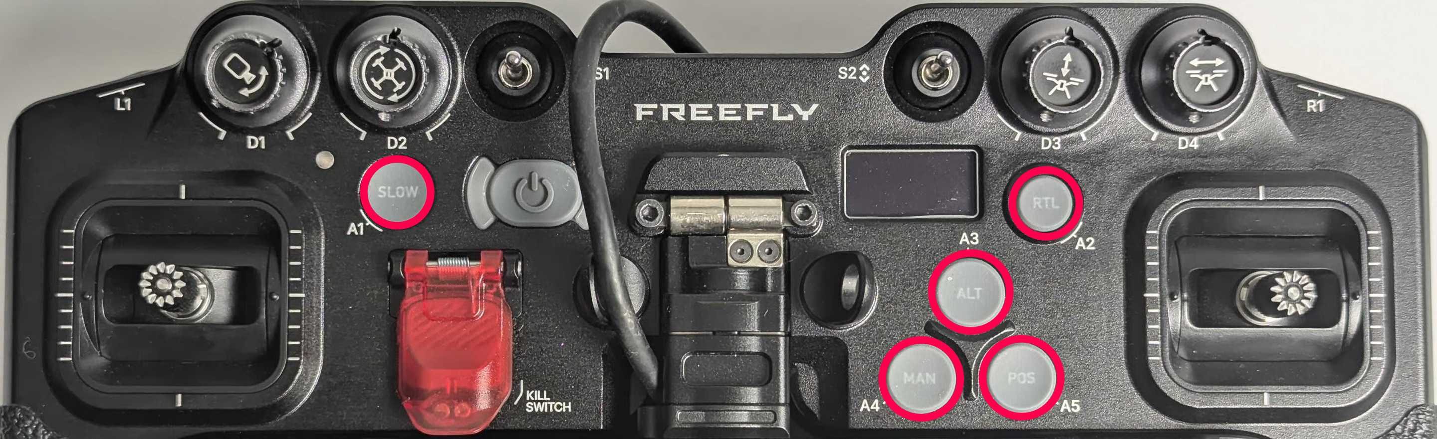
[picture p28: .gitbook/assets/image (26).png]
<figure><figcaption></figcaption></figure>

{% hint style="success" %}
Manual Mode may be necessary to react to emergency situations. Pilots should be proficient in Manual Mode. Position, Altitude, and Return Mode are assistive only and are not a replacement for pilot skill and preparedness.
{% endhint %}

{% hint style="warning" %}
Always neutralize the control input sticks on the pilot handset when switching between control modes to prevent unexpected aircraft movement.
{% endhint %}

***

## Pilot-Controlled Modes

{% tabs %}
{% tab title="Position" %}
<figure><figcaption><p>Position Mode Button on Pilot Pro</p></figcaption></figure>

In Position Mode, when sticks are centered, the aircraft maintains its position over a point on the ground and holds altitude, correcting for disturbances.

**Controls:**

* Pitch/Roll stick → commands ground speed (forward, backward, left, right)
* Throttle stick up/down → commands vertical speed
* Throttle stick left/right → commands yaw rate

{% hint style="info" %}
Position Mode requires a strong GPS signal. If signal deteriorates (near buildings, under tree cover), the aircraft will automatically revert to Altitude Mode.
{% endhint %}

{% hint style="danger" %}
Flight in areas of degraded GPS is not recommended. Automatic reversion to Altitude Mode can cause unexpected changes in flight behavior.
{% endhint %}
{% endtab %}

{% tab title="Altitude" %}
<figure><figcaption><p>Altitude Mode Button on Pilot Pro</p></figcaption></figure>

Similar to Position Mode, but the aircraft only holds altitude—not lateral position. Alta X Gen2 will drift with the wind and will not hold a fixed point without pilot input.

{% hint style="info" %}
The aircraft holds altitude above Mean Sea Level (MSL) by default. It is not aware of terrain height changes without additional configuration.
{% endhint %}
{% endtab %}

{% tab title="Manual" %}
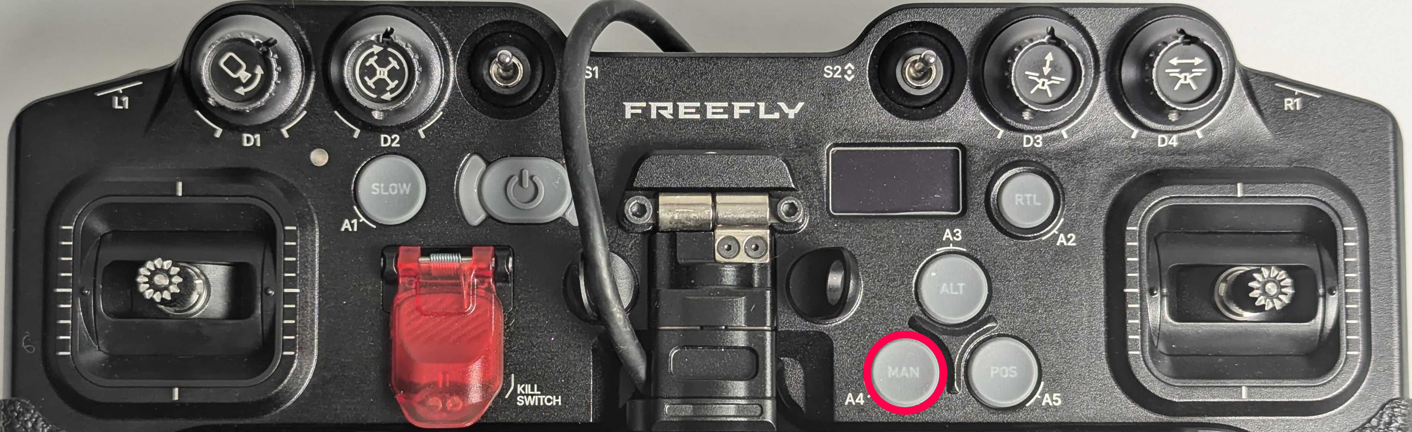
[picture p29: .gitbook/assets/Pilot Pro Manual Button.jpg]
<figure><figcaption><p>Manual Mode Button on Pilot Pro</p></figcaption></figure>

In Manual Mode, the aircraft attempts to remain level when sticks are centered but will drift with wind. Constant throttle adjustment is required to hold altitude.

**Controls:**

* Pitch/Roll stick → commands aircraft angle (tilt)
* Throttle stick → controls motor speed directly
* Throttle left/right → commands yaw rate

**Manual Mode Settings**

The hover throttle setting controls thrust produced when the throttle stick is centered.

* Default: \[TBD]% will hover with no payload
* Approximately \[TBD]% will hover with \[TBD] grams of payload

Adjust hover throttle setting in AMC:

* Switch to Advanced Mode by repeatedly tapping on the AMC icon in the top-left-hand corner of the app.
* Go to Vehicle Setup → Tuning → Hover Throttle<br>
{% endtab %}

{% tab title="Position Slow" %}
<figure><figcaption><p>Position Slow Mode Button on Pilot Pro</p></figcaption></figure>

Position Slow acts like Position Mode but allows finer control over movement speed using the dials on Pilot Pro. Useful for tower inspections or cinematic shots.

{% hint style="info" %}
The gimbal's dial (left) is always active regardless of mode
{% endhint %}
{% endtab %}
{% endtabs %}

***

## Autonomous Modes

{% tabs %}
{% tab title="Return" %}
<figure><figcaption><p>Return Mode Button on Pilot Pro</p></figcaption></figure>

Return Mode commands Alta X Gen2 to:

1. Climb to the Return Altitude
2. Fly back to the Home Point in a straight line
3. Land

**Key settings:**

* **Return Altitude:** Set it in AMC → Vehicle Setup → Safety. If already above Return Altitude, aircraft maintains current altitude.
* **Home Point:** Automatically set to GPS coordinates where aircraft was armed. Resets every arm.

By default, Return Mode is activated automatically by some Failsafes.

{% hint style="warning" %}
Before every flight, think through the path the aircraft will take if Return Mode activates. Activating Return Mode while under an obstacle lower than Return Altitude will cause a collision.
{% endhint %}

{% hint style="info" %}
You can exit Return Mode by pressing another flight mode button.
{% endhint %}

#### **Return behavior based on position:**

In most cases, RTL mode will travel to the predetermined RTL altitude, travel over the home point, and automatically descend to land. However, if the aircraft is close to the home point, the behavior will be slightly different in order to save time and reduce the amount of distance the aircraft will need to move.

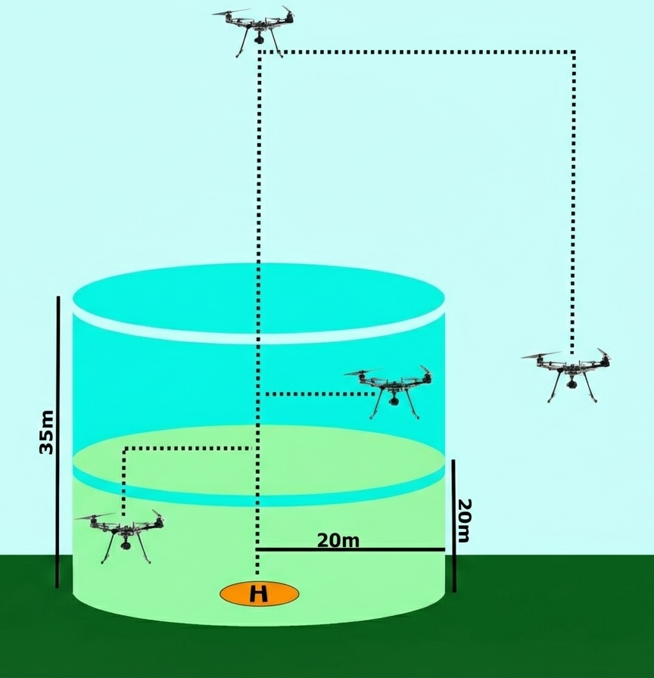
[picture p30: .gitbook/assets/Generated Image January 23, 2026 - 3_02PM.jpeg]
<figure><figcaption></figcaption></figure>

| Position | Behavior |
| --- | --- |
| Directly over home point | Land without gaining altitude |
| Within a few meters of home | Move over home point, land |
| <20m altitude AND <20m distance | Climb to 20m, move over home, land |
| 20-35m altitude AND <20m distance | Maintain altitude, move over home, land |
| >35m altitude OR >20m distance | Climb to Return Altitude, move over home, land |
{% endtab %}

{% tab title="Takeoff" %}
Takeoff Mode arms the aircraft, climbs to the Takeoff Altitude, and enters Hold Mode (hover in place).

Can be engaged via AMC Fly view button or as the first command in a mission.

{% hint style="info" %}
Takeoff Mode requires a GPS lock.
{% endhint %}
{% endtab %}

{% tab title="Landing" %}
#### Landing Mode

Landing Mode descends and lands directly below current position. Aircraft disarms after touchdown.

Engage via AMC Fly view button (hold to confirm).

Also used as the last command in missions or triggered by some failsafes.

{% hint style="warning" %}
Land Mode requires GPS when engaged manually. If engaged by failsafe without GPS, aircraft descends like Altitude Mode and may drift.
{% endhint %}
{% endtab %}

{% tab title="Mission" %}
Mission Mode executes a predefined autonomous waypoint mission uploaded via AMC.

See AMC documentation for:

* [Planning a mission](https://freefly.gitbook.io/astro-public/astro/pilots-operating-handbook/software/auterion-mission-control/amc-plan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)
* [Flying a mission](https://docs.auterion.com/auterion-mission-control/fly/flying-a-mission)
* [Remove a mission from the aircraft](https://docs.auterion.com/auterion-mission-control/plan/plan-ui-overview#file-sync-tools)

{% hint style="danger" %}
Starting a mission can cause the aircraft to arm and take off without further input. Ensure area is clear.
{% endhint %}

{% hint style="info" %}
If a mission is interrupted (e.g., pilot switches to Position), AMC will prompt to resume. If no prompt, use Action Menu → Resume Mission.
{% endhint %}

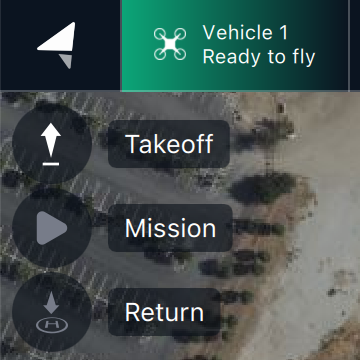
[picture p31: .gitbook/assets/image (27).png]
<figure><figcaption></figcaption></figure>

{% hint style="info" %}
Aircraft must have GPS lock before takeoff to start a mission. If armed without GPS lock, Mission Mode will be unavailable until landing and rearming with GPS.
{% endhint %}
{% endtab %}
{% endtabs %}

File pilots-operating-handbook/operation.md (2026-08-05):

---
icon: drone-front
---

# Flight Part 2 - Operation

{% hint style="warning" %}
Make sure you understand Alta X Gen2's [Emergency Procedures](emergency-procedures.md) and can operate in [Manual Mode](flight-modes.md#manual) before taking flight.
{% endhint %}

## Flight Checklists

Below is our recommended checklist and emergency procedures, which covers the main considerations you need to be aware of before, during, and after operation.

{% file src="../.gitbook/assets/Alta X Gen2 Checklists and EPs - V1.pdf" %}

We also offer this checklist as a [Google Sheet template](https://docs.google.com/spreadsheets/d/1JPw9swa9Qgde6kN0BwlyTe5oQbtJ-K0krS4xsyxAoW8/edit?usp=sharing) for customization to your company's procedures, workflow, or region.

***

## Before Flight

#### Powering On Pilot Pro

* Press the power button once to wake it up and to check its charge level. Press a second time to power it on.
* Once the Tablet boots, the Pilot Pro App will open. Switch to AMC app for flight.

#### Powering On Alta X Gen2

* Alta X Gen2 is powered by connecting the Tattu batteries — no power button required.
* **For ground/bench operations:** Connect one battery using the fused cable. This prevents arming as a safety mechanism.
* **For flight:** Connect two batteries directly (no fused cable). Both batteries power on automatically when connected.

{% hint style="warning" %}
Bench mode (single battery + fused cable) is not a substitute for the absolute safety of removing propellers.
{% endhint %}

#### Checking Battery Levels

* Once connected, AMC displays Alta X Gen2 battery level in the status bar. Tap the battery indicator to see more details, such as per-battery values.

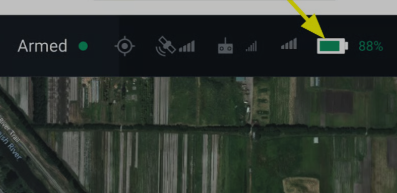
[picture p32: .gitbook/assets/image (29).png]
<figure><figcaption></figcaption></figure>

{% hint style="info" %}
The LED indicator on the Tattu battery itself can be inaccurate. For accurate state of charge, check via the Tattu Smart Charger or AMC.
{% endhint %}

***

## Arming and Disarming

Alta X Gen2 has two states:

| State | Definition | Boom LEDs |
| --- | --- | --- |
| Disarmed | Safe, propellers will not spin | Dim |
| Armed | Ready to fly, propellers will spin | Bright |

* Alta X Gen2 can arm with or without GPS.
* Pro Tip: Wait for GPS lock even if you don't plan to use Position Mode because Return Mode relies on GPS.
* Missions with a takeoff command will arm automatically when initiated.

{% hint style="danger" %}
Before arming, ensure people and other obstacles are clear of the propellers.
{% endhint %}

#### Arming and Disarming with Sticks (Mode 2)

| Action | Input |
| --- | --- |
| Arming | Hold throttle stick down and right for 2 seconds |
| Disarming | After landing, continue holding throttle stick down for 2 seconds |

* You cannot disarm via sticks while in flight. Use Emergency Stop if needed.
* Use only the throttle stick. Alta X Gen2 does not respond to two-stick arming gestures (i.e. DJI arming gesture)
* The pilot's handset default configuration is [Mode 2](https://docs.px4.io/master/en/getting_started/rc_transmitter_receiver.html#types-of-remote-controls).

#### Automatic Disarm

Under these conditions, Alta X Gen2 will automatically disarm.

| Condition | Behavior |
| --- | --- |
| Ground timeout | If armed but idle on ground for 10 seconds, auto-disarms |
| Return or Land mode | After detected landing, disarms after 2 seconds |

***

## Taking Off

Position Mode is recommended for takeoff in most cases.

For 5 seconds after takeoff, maximum pitch and roll angles are limited to 12 degrees.

> **Tip:** After takeoff, promptly climb above 3 meters (10 feet) to exit ground effect and avoid snagging landing gear.

#### In Position or Altitude Mode

1. After arming, allow throttle stick to return to center—propellers remain at idle
2. When ready, raise throttle stick
3. Propellers spin up and aircraft takes off

#### In Manual Mode

1. After arming, hold throttle stick straight down (no yaw input)
2. Slowly raise throttle—propellers accelerate immediately
3. As throttle approaches mid-point, aircraft will lift off
4. Continue raising throttle for a brisk takeoff

***

## Landing

Position Mode is recommended for landing in most cases.

{% hint style="danger" %}
Do not hand catch Alta X Gen2. Land on hard, flat surfaces only. Hand catching can result in serious injury or death.
{% endhint %}

In Position and Altitude Modes

* Below 7 meters altitude, maximum descent rate is reduced to 0.7 m/s (from 2 m/s).
* Below 2 meters altitude, maximum pitch/roll angle is reduced to 12 degrees to prevent tip-overs.

Alta X Gen2 disarms automatically after detecting landing. Landing detection brings together input from several sensors to determine when it is safe to disarm.

{% hint style="warning" %}
If landing is not detected (props keep spinning after touchdown), see Emergency Procedures for Landing Detector Failure.
{% endhint %}

#### Landing best practices

{% tabs %}
{% tab title="Landing In Position Mode" %}
1. Hover above 2 meters over landing spot
2. Pull throttle straight down—no pitch, roll, or yaw input
3. Landing sensor manages descent speed
4. After touchdown, hold throttle down until disarm

{% hint style="warning" %}
Pitch, Roll, or Yaw commands very near the ground can cause crashes or tip-overs.
{% endhint %}
{% endtab %}

{% tab title="Landing In Altitude Mode" %}
1. Hover above 2 meters over landing spot
2. Use minimal pitch/roll to control lateral drift
3. Pull throttle down—autopilot controls descent rate
4. After touchdown, hold throttle down until disarm
{% endtab %}

{% tab title="Landing In Manual Mode" %}
Landing in Manual Mode is different than Position or Altitude Mode because the pilot is responsible for managing vertical _and_ lateral velocity.

1. Hover above 2 meters over landing spot
2. Use minimal pitch/roll to minimize lateral speed
3. Reduce throttle to descend slowly
4. Near ground (in ground effect), reducing throttle further is often needed to keep the aircraft descending
5. After touchdown, reduce throttle to zero promptly
6. Hold throttle down until disarm and propellers stop completely
{% endtab %}
{% endtabs %}

{% hint style="danger" %}
While Alta X Gen2 will recognize that the battery is low and perform a failsafe action (return to launch by default), the aircraft has no context of situations that might prevent a safe landing before the battery is exhausted. For instance, if the aircraft is several miles away from the RTL point when the failsafe is triggered, there is a chance that there won't be enough battery life to return.\
\
It is the pilot's responsibility to determine the appropriate time for a battery change and to ensure the aircraft is safely grounded.
{% endhint %}

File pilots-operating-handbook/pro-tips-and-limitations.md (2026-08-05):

---
icon: lightbulb
---

# Pro-tips and Limitations

It is possible to operate Alta X Gen2 close to the limits of performance by maintaining awareness of the performance envelope, how the aircraft behaves if the limits are exceeded, and best practices for operating in harsh environments.

This page reflects the limitations of the most current version. As the Alta X Gen2 platform matures, limitations are likely to change.

***

## Radio Range and Interferences 

Operating with a weak signal, whether due to interference or long range, can cause loss of link with the aircraft, which will engage failsafes. If you anticipate a weak signal situation, double-check that failsafes are set appropriately.

### Range 

The range of Herelink and Doodle radios on Alta X Gen2 is approximately 2 km in ideal conditions, assuming there are no interferences and the antennas are positioned correctly.

### Antenna Positioning 

This is one of the simplest to miss and impact the range of the flight

**Pilot Pro**

Both the Doodle and Herelink radio modules on Pilot Pro use two blade antennas that are omni directional. It is important to follow these basic guidelines:

* Antennas should both point in the same direction.
* Antennas should point towards ground, so that the long side of the antennas are pointed the drone.

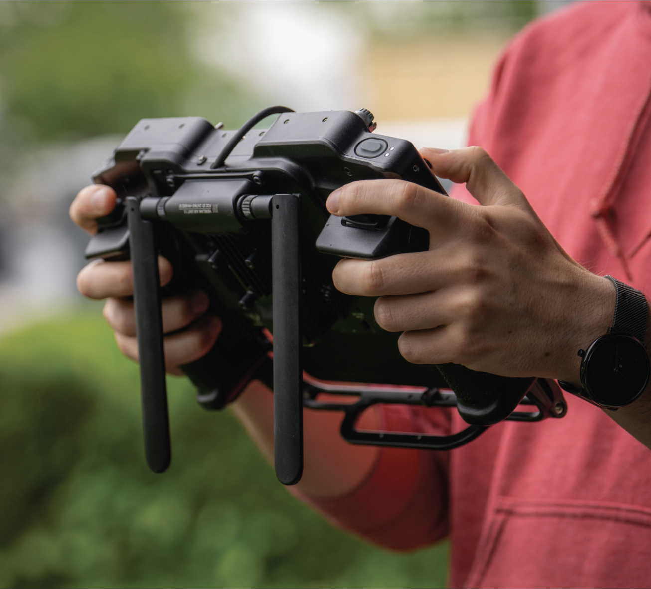
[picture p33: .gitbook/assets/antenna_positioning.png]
<figure><figcaption></figcaption></figure>

### Interferences 

Range can be reduced by radio interference from other sources like WiFi networks. Obstacles like trees and buildings in close proximity to the controller or Alta X Gen2, as well as directly between the two, can dramatically reduce range.

#### Multiple Aircraft 

* Alta X Gen2's Doodle radio configuration runs on dedicated peer to peer channels. In order to fly multiple Alta X Gen2 or Astro aircraft in the same airspace, make sure to scan channels and then set each Doodle to a different channel.
* Alta X Gen2's Herelink radios are channel hopping by default. 4 aircraft can fly simultaneously in the same airspace in practice. If more aircraft are present, interference can cause loss of radio link and control.

***

## Environment

### Temperature

Alta X Gen2 can operate between -20 and 50 C. Position mode and survey flying are normal throughout the range. However, care is needed to operate at low and high temperatures.

{% tabs %}
{% tab title="Tips for operating in hot environments" %}
At high temperatures, the limiting factor is battery temperatures. AMC will display a warning if the batteries become too hot. Heed the warnings! Alta X Gen2 operates normally in forward flight up to 15 m/s with a full payload.

Cooling air is your friend. The system gets much more cooling air in forward flight than in a hover. Overheat errors may occur when hovering because there is less airflow, or when flying aggressively because heating increases with current.

Batteries may require cooling before charging. Bring an extra set of batteries and chargers to enable continuous flying.

Keep the equipment out of prolonged direct sunlight.
{% endtab %}

{% tab title="Tips for operating in cold environments" %}
At low temperatures, the battery cell temperature is the key limiting factor. When the cells themselves are below 10 °C (ambient air can be down to -20 °C), the batteries' performance may be reduced. If this happens, low battery failsafes (RTL and Land) will be triggered, causing the aircraft to climb or descend suddenly.

These failsafes can be overridden by selecting another flight mode. The battery will not cut off power output in the air, however low temperatures generally reduce capacity which will reduce flight time.

If the batteries are 10 °C or warmer at the start of a flight, heating from discharge will keep them warm enough to fly.

To keep batteries warm, charge them in a heated environment and store them in an insulated container (a cooler works well).

**In rare cases propellers can experience icing, this occurs when ice begins to form on the tips and underside of the blades due to temperature and humidity. This will cause the props to become unbalanced, increasing drag and reducing lift. Flying with iced blades can be dangerous and is not advised.**
{% endtab %}
{% endtabs %}

### Ingress

Alta X Gen2 is designed to withstand light rain ([IP43 rated](../specs/tech-specs.md#environmental)). Ensure the IO panel, voltage regulator, and USB covers are installed when flying in dusty or wet conditions.

When flying in rain, we have seen some instances where water ingresses to the battery through the balance lead port. This may cause the battery’s BMS to report incorrect information. To prevent this, we include stickers to cover the balance port on the batteries. See [here](../other-user-manuals/ecosystem/batteries-and-charging.md#installing-the-battery-balance-port-stickers) for instructions on installing them.

## Travel and Shipping

Alta X case outside dimensions: 33.75 x 28.5 x 16.25 inches

Alta X loaded case weight: 77 lb / 35 kg

* Payload mount rails and smart dovetail fit in the case installed on Alta X Gen2.
* Cinema isolator does not fit in the Alta X Gen2 case.

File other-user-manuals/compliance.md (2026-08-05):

---
icon: gavel
---

# Compliance

## FAA Remote Identification (RID)

Alta X Gen2 comes with Standard Remote ID built in.

Registration

1. Find your Remote ID Serial Number\
   \- Connect Alta X Gen2 via USB and navigate to the Settings page (10.41.1.1)\
   \- Locate the Skynode Serial Number (e.g., 132000209)

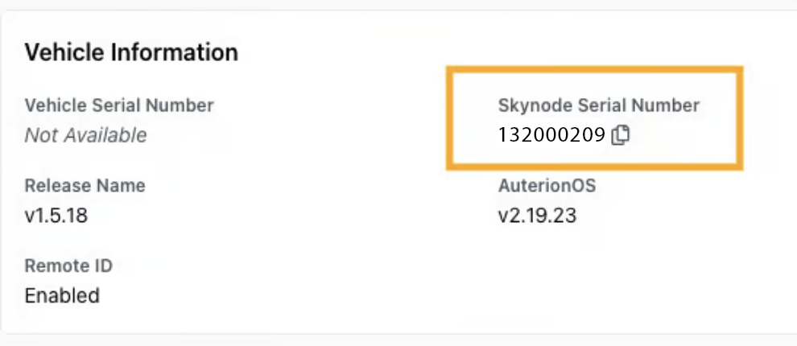
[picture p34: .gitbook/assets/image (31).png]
<figure><figcaption></figcaption></figure>

\- Prefix with **18179** to get your FAA Remote ID Serial Number (e.g., 18179132000209)

2. Register at [https://faadronezone.faa.gov](https://faadronezone.faa.gov/)\
   \- Log in or create an account\
   \- Select 'Drone Owners and Pilots Dashboard'\
   \- Select 'Manage Device Inventory' → 'Add Device'
3. Affix a label to your drone\
   \- Print a label indicating "FAA Standard Remote ID Compliant"\
   \- Label must be in English, legible, prominent, and permanently affixed

### &#x20;

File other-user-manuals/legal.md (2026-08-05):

---
icon: building-columns
---

# Legal

## Disclaimer and Warning

Please read this disclaimer and warning carefully and review the ALTA X GEN2 Aircraft Flight Manual (AFM) prior to flight. If you have any questions, please contact support@freeflysystems.com prior to using the ALTA X GEN2. By using ALTA X GEN2, you acknowledge that you have read, understand and agree to this disclaimer. You agree that you are solely responsible for your conduct while using ALTA X GEN2, and for any direct or indirect consequences that may result from its use. You agree to only use ALTA X GEN2 for proper purposes that are in accordance with local and airspace rules and regulations.

* ALTA X GEN2 is not a toy and should be operated with extreme care, as improper operation can cause damage to property, serious personal injury or death.
* As with any multi-rotor aircraft, ALTA X GEN2 is a complex and technical machine. Novice pilots should invest sufficient time on a flight simulator and seek training from an experienced pilot prior to operation. The ALTA X GEN2 Aircraft Flight Manual and a flight simulator are no substitute for training with an experienced pilot, particularly when it comes to learning how to safely operate ALTA X GEN2. Novice pilots should never fly without the supervision of an experienced pilot.
* Always check ALTA X GEN2 and its components prior to operation.
* Always maintain a safe distance from ALTA X GEN2 when in use.
* Never attempt to touch ALTA X GEN2 when the propellers are moving.
* Never fly ALTA X GEN2 over or around people, power lines or other aircraft.
* Never fly with any propellers that have visible imperfections or damage.
* Always keep children and animals a safe distance away from ALTA X GEN2 when in use and when changing configurations.
* Only use propellers supplied by Freefly Systems that are designed for use on ALTA X GEN2.
* Always remove the propellers or power ALTA X GEN2 using a low power source when making a change to the configuration of ALTA X GEN2 to prevent propeller strikes in the event of unintentional motor starts.
* Always test ALTA X GEN2 with the propellers removed to make sure that the motors are spinning in the correct direction and that the motor assignment is correct with respect to the Autopilot flight controller. If you have either of these wrong, the ALTA X GEN2 will be uncontrollable and dangerous.
* It is your responsibility to perform a full system check of ALTA X GEN2 prior to every flight.
* It is your responsibility to learn how to safely operate ALTA X GEN2 and to adhere to all applicable rules and regulations.
* Fly at your own risk.
* ALTA X GEN2 is a tuned system with custom components selected for each application. Modification, removal, or substitution of ALTA X GEN2 components will void the warranty and can lead to unsafe operating conditions.

## Limitations of Liability

IN NO EVENT SHALL FREEFLY BE LIABLE TO BUYER FOR ANY INDIRECT, CONSEQUENTIAL, PUNITIVE, INCIDENTAL, OR SPECIAL DAMAGES, OR ANY DAMAGES WHATSOEVER RESULTING FROM THE USE OF ALTA X GEN2 OR FROM LOSS OF USE, DATA OR PROFITS (HOWEVER CAUSED AND UNDER ANY THEORY OF LIABILITY), EVEN IF FREEFLY HAS BEEN ADVISED OF THE POSSIBILITY OF SUCH DAMAGES. IN NO EVENT SHALL FREEFLY’S LIABILITY FOR A PRODUCT (WHETHER ASSERTED AS A TORT CLAIM, A CONTRACT CLAIM OR OTHERWISE) EXCEED THE AMOUNTS PAID TO FREEFLY FOR SUCH PRODUCT. NOTWITHSTANDING ANYTHING HEREIN, IN NO EVENT SHALL FREEFLY’S LIABILITY FOR ALL CLAIMS ARISING OUT OF OR RELATING TO THIS AGREEMENT EXCEED THE AMOUNTS PAID BY BUYER TO FREEFLY FOR PRODUCT IN THE LAST TWELVE (12) MONTHS. IN NO EVENT WILL FREEFLY BE LIABLE FOR COSTS OF PROCUREMENT OR SUBSTITUTE GOODS BY BUYER. THE LIMITATIONS SET FORTH HEREIN SHALL APPLY TO ALL LIABILITIES THAT MAY ARISE OUT OF THIRD-PARTY CLAIMS AGAINST BUYER. THESE LIMITATIONS SHALL APPLY NOTWITHSTANDING ANY FAILURE OF ESSENTIAL PURPOSE OF ANY LIMITED REMEDY. Freefly shall not be liable for damages or injuries incurred directly or indirectly from the use of ALTA X GEN2 including, but not limited to, the following situations:

* Failure of the operator to follow proper instructions and safety warnings found at www.freeflysystems.com.
* Failure of the operator to understand and operate the aircraft within the operating limitations described in this manual.
* Failure of the operator to follow onboard safety warnings while using ALTA X GEN2.
* Failure of the operator to follow and comply with local rules and regulations.
* Failure of the operator to follow and comply with the local communications law.
* Failure of the operator to inspect ALTA X GEN2 and its components prior to operation.
* Failure of the operator to properly maintain and/or service ALTA X GEN2 through an authorized Freefly Service Center with genuine ALTA X GEN2 parts.
* Use of third-party products on ALTA X GEN2.
* Use of ALTA X GEN2 in a physically or mentally impaired capacity.
* Use of ALTA X GEN2 without sufficient training.
* Use of ALTA X GEN2 in unsafe conditions, including but not limited to, bad or severe weather, such as rain, wind, snow, lightning, dust storms, etc., or in areas of magnetic or radio interference, such as power stations, broadcasting and cell phone towers, government prohibited airspace, etc.
* Improper operation, misjudgment or risky behavior while using ALTA X GEN2.
* Infringement of third party data, audio, or video rights recorded when using ALTA X GEN2.

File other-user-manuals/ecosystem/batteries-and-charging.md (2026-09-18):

# Batteries and Charging

Alta X Gen2 is designed to fly with two Tattu Plus 1.0 12S 16Ah LiPo batteries. The battery voltage bus runs between 36 and 50.4 volts.

In an emergency, the aircraft is capable of flying and landing safely on one battery.

It is not possible to power the aircraft via the USB-C port.

{% hint style="warning" %}
Battery hot swaps are not recommended. Please power off the aircraft by disconnecting both batteries when swapping packs to ensure ideal performance and battery lifespan.
{% endhint %}

## Charger

The Tattu TA3200 smart charger is the recommended charger. It supports dual battery charging, and single connector charging through the AS150U connector.

<figure><figcaption></figcaption></figure>

For more information, see the charger's [user manual](https://www.genstattu.com/content/TA3200TA3200HVManual.pdf).

***

## Batteries

Alta X Gen2 is designed to operate with two Tattu Plus 1.0 12S 16Ah smart batteries with AS150U connectors.

<figure><figcaption></figcaption></figure>

***

## Installing the Battery Balance Port Stickers

When flying in rain, we have seen some instances where water ingresses to the battery through the balance lead port. This may cause the battery’s BMS to report incorrect information. To prevent this, we include stickers to cover the balance port on the batteries. If you need more stickers, contact [Freefly Support](https://freeflysystems.com/contact).<br>

**You will need:**

* Tattu Plus 1.0 12S 16Ah smart battery
* Balance port sticker
* Alcohol swab (included with the sticker)

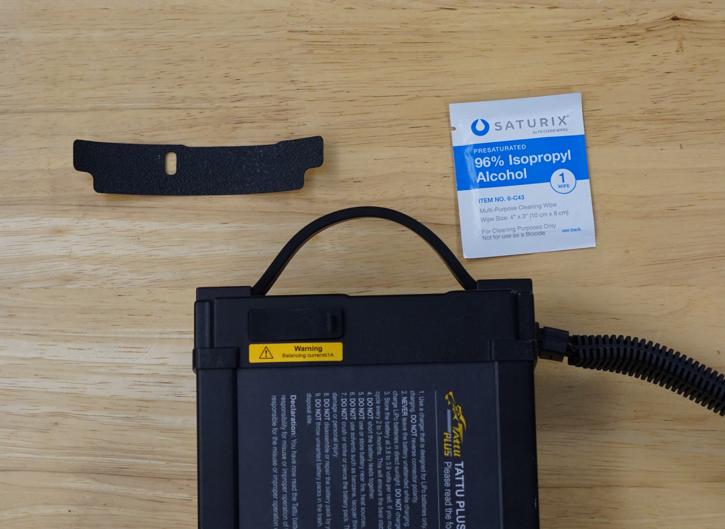
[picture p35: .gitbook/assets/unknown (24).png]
<figure><figcaption></figcaption></figure>

1. On the Tattu Plus 1.0 12S 16Ah smart battery, fully seat the rubber cover on the balance port and remove the warning sticker.

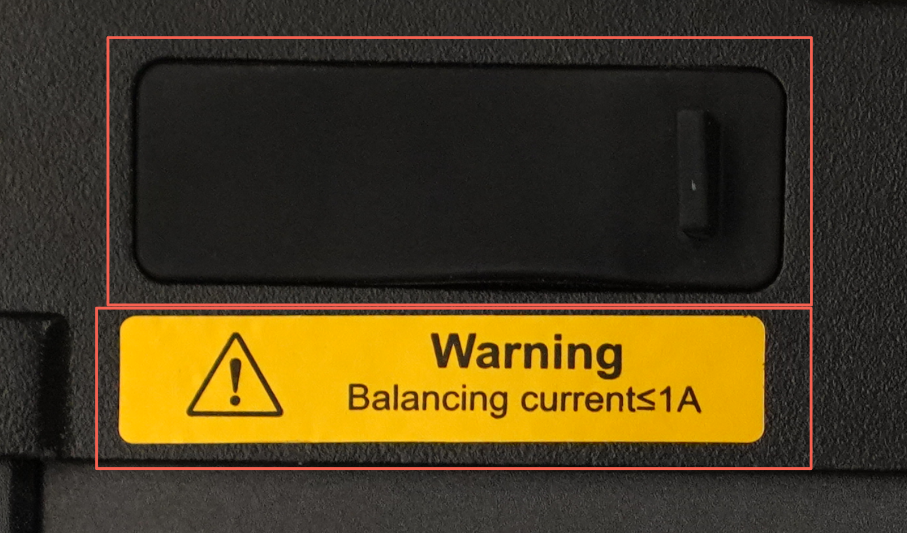
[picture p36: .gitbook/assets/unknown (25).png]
<figure><figcaption></figcaption></figure>

<br>

2. Use the included alcohol wipe to clean off any dust, dirt, or residue from the area marked below.

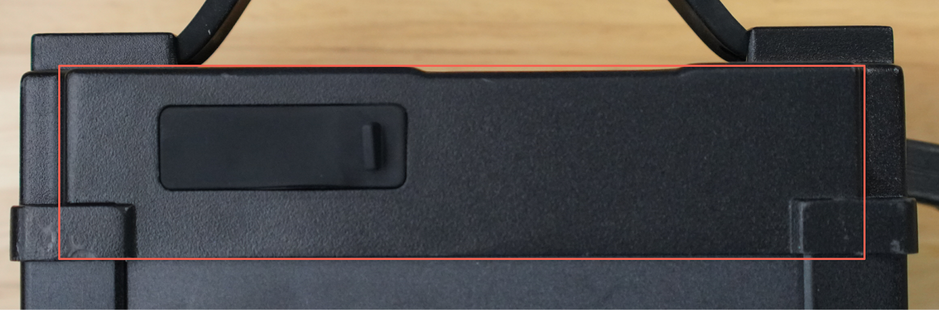
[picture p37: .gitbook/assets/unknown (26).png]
<figure><figcaption></figcaption></figure>

3. Once dry, apply the sticker over the cover with the tab poking out through the hole in the sticker. Use firm pressure to ensure adhesion.

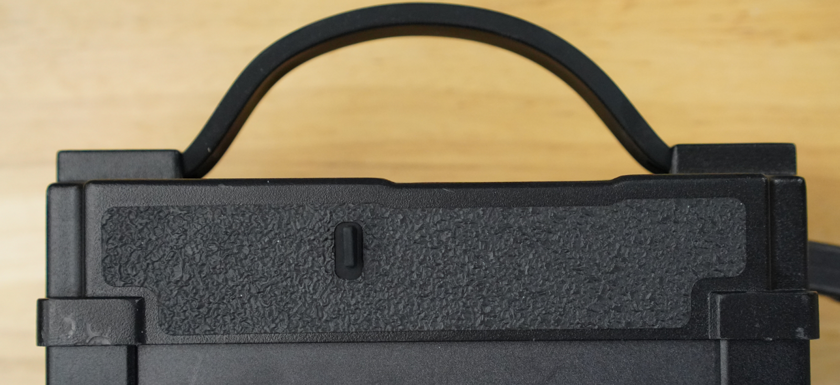
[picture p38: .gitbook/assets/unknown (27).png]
<figure><figcaption></figcaption></figure>

***

## Switching Battery Modes

{% hint style="danger" %}
This is an advanced feature and not recommended for normal use.
{% endhint %}

Alta X Gen2 ships in smart battery mode. This mode enables the aircraft to communicate with the batteries' BMSs for:

* Better flight time estimation
* Battery fault monitoring
* Requires two batteries to arm

We recommend leaving Alta X Gen2 in this default configuration and flying with the recommended smart batteries.

The battery mode can be changed to disable smart battery mode. This enables flying with other batteries (like Alta X Gen1 flight batteries) or non-traditional power systems. To change this, follow the instructions below to change the mode.

**To change the mode:**

1. Power on Alta X Gen2 with one battery and the fused cable.
2. Power on Pilot Pro or connect a PC with a USB-C cable.
3. Open AMC, then press the upper left icon 7 times to enter Advanced mode.
4. Click the icon again to open the side menu, then navigate to Advanced -> Parameters.
5. Enter "FF\_AX2\_BAT\_CFG" in the search box, then select the FF\_AX2\_BAT\_CFG parameter.
6. Enter the new value, the click Save.
   1. To enable Smart Battery mode (enabled by default) set this parameter to "2 Smart Batteries with UAVCAN". If entering the raw value, it is `2`
   2. To disable Smart Battery mode set this parameter "1 or 2 Dumb Batteries". If entering the raw value, it is `0`
7. Once saved, reboot the aircraft.

***

## Replacing the fuse in the fused cable

Alta X Gen2 includes an inline power cable with a protective fuse designed for ground operations. Install it between a single battery and the aircraft when performing maintenance, updates, configuration, or other work near the drone. In the event that the fuse blows, it can be replaced with a 5A mini automotive blade fuse.

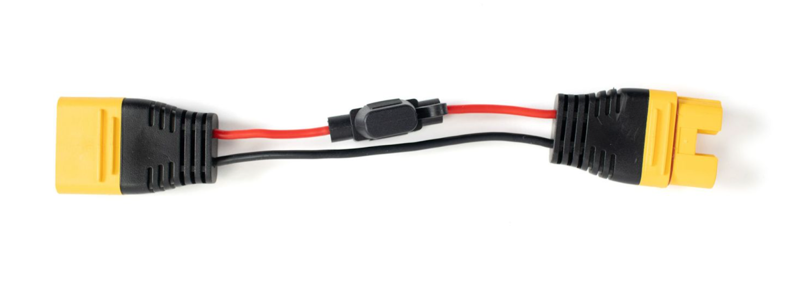
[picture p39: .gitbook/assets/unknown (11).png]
<figure><figcaption></figcaption></figure>

1. Open the rubber cover in the fused cable.

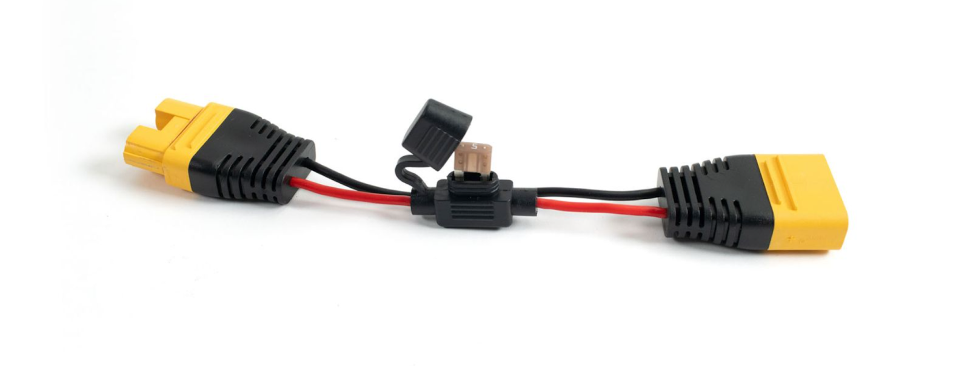
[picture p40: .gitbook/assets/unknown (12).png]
<figure><figcaption></figcaption></figure>

2. Remove the old fuse.

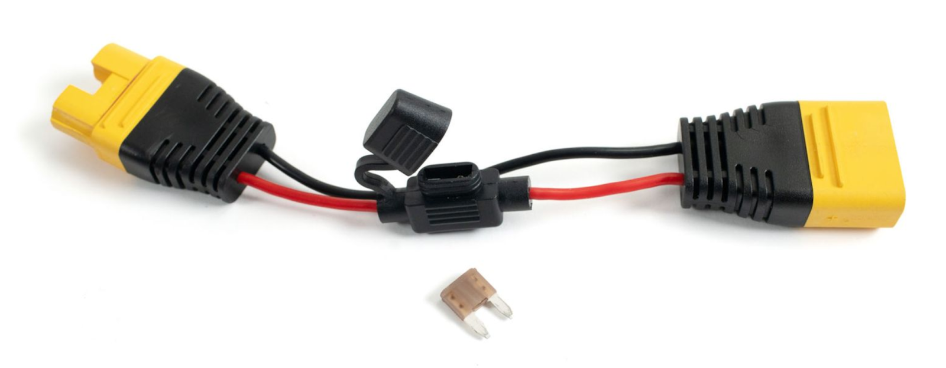
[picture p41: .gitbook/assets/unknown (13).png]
<figure><figcaption></figcaption></figure>

3. Replace with a 5A mini automotive blade fuse. Note: Do not use a higher current rating fuse in this cable.

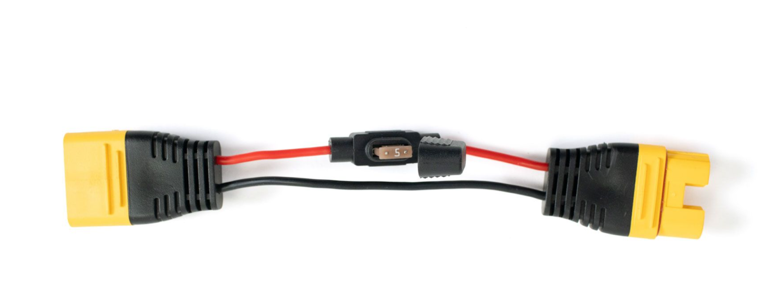
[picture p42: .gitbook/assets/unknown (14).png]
<figure><figcaption></figcaption></figure>

4. Close the rubber cover.

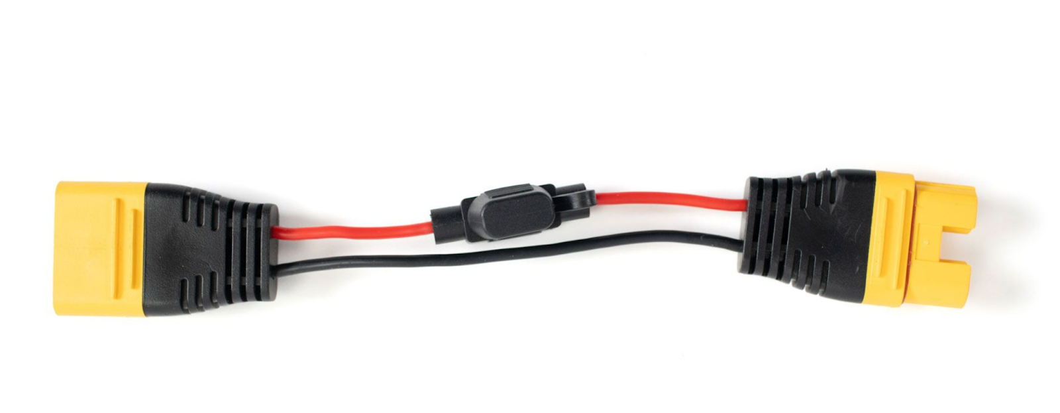
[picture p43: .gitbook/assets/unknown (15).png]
<figure><figcaption></figcaption></figure>

<br>

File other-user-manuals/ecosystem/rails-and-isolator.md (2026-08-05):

# Rails and Isolator

### Removing or replacing the rails and isolator

Alta X Gen2 comes with 12mm rails and the Smart Dovetail isolator. To remove them:

1. Place Alta X Gen2 upside down on a clean, flat surface.

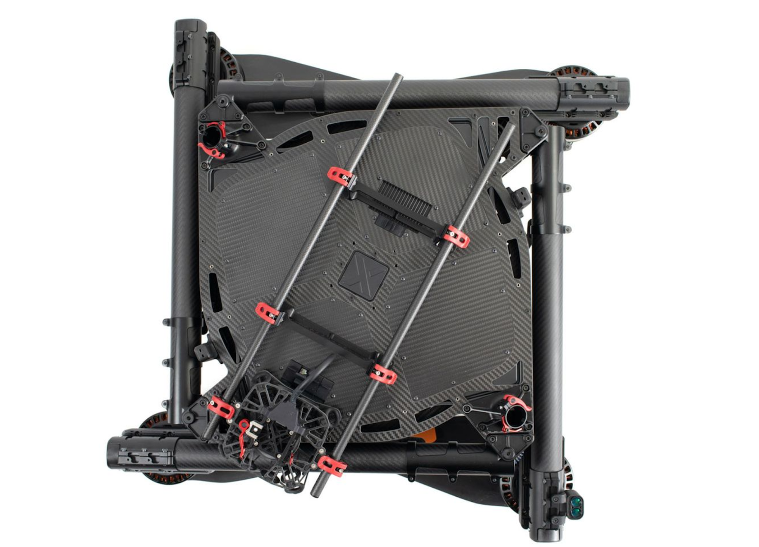
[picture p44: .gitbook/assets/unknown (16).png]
<figure><figcaption></figcaption></figure>

2. Unplug the Smart Dovetail from Alta X Gen2’s IO panel. Grip the connector and depress the locking tab then gently unseat.

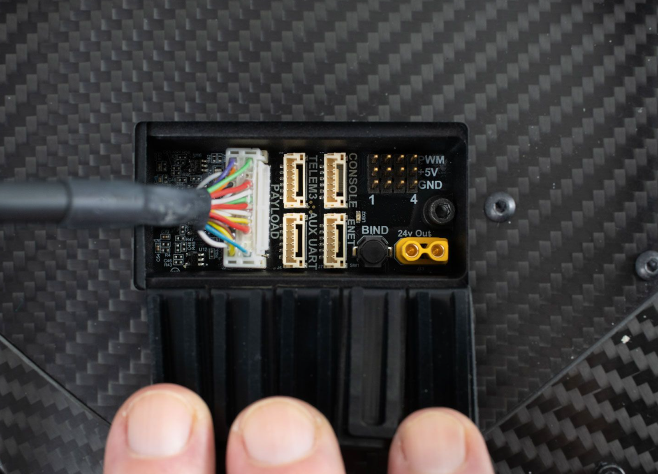
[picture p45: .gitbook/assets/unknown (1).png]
<figure><figcaption></figcaption></figure>

<br>

3. Loosen the red levers clamping the isolator to the rails.

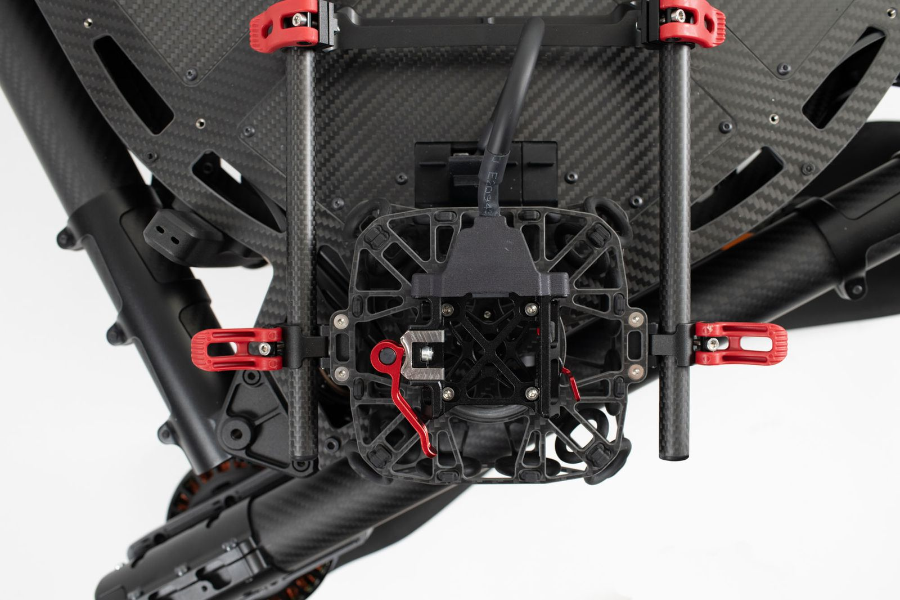
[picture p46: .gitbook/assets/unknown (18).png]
<figure><figcaption></figcaption></figure>

4. Slide the isolator off of the rails or open the levers and rotate the isolator to remove it from the rails.
5. Loosen the red rail tube levers then slide out the rails.
6.  Using a 2.5mm hex driver, remove the four M3x10 combo head screws attaching the rails to the bottom of Alta X Gen2.

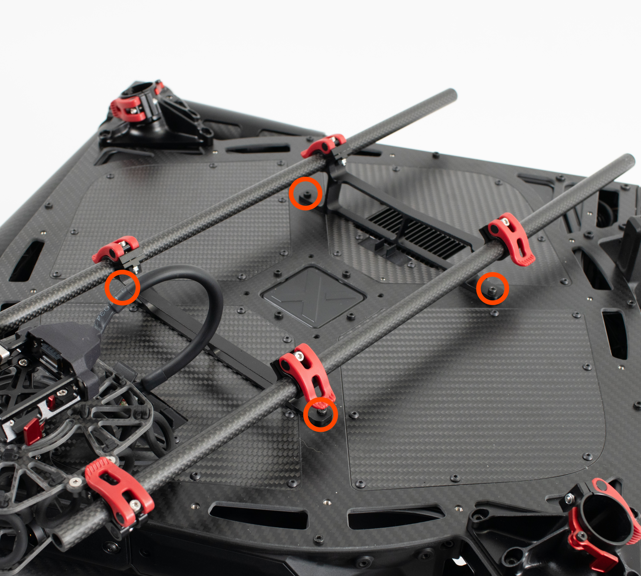
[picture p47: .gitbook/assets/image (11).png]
    <figure><figcaption></figcaption></figure>

<br>

**To reinstall the rails and/or isolator:**

1. Place Alta X Gen2 upside down on a clean, flat surface.

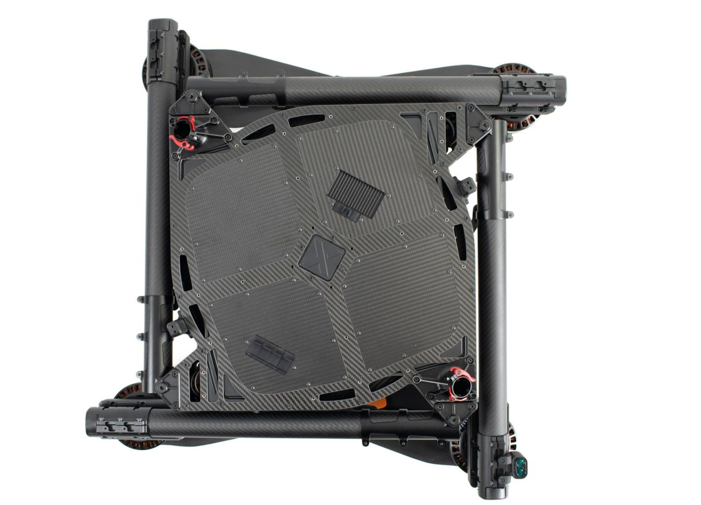
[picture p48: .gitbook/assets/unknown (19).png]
<figure><figcaption></figcaption></figure>

2. Attach the two rail adapters to the bottom chassis with 4x M3x10 combo head screws. Only loosely tighten these.
3. Open the locking levers on the adapters and slide in the two 12x500mm tubes. Sliding in the tubes will align the adapters to be parallel.
4.  Tighten the four screws fully, then close the locking levers to clamp the tubes.

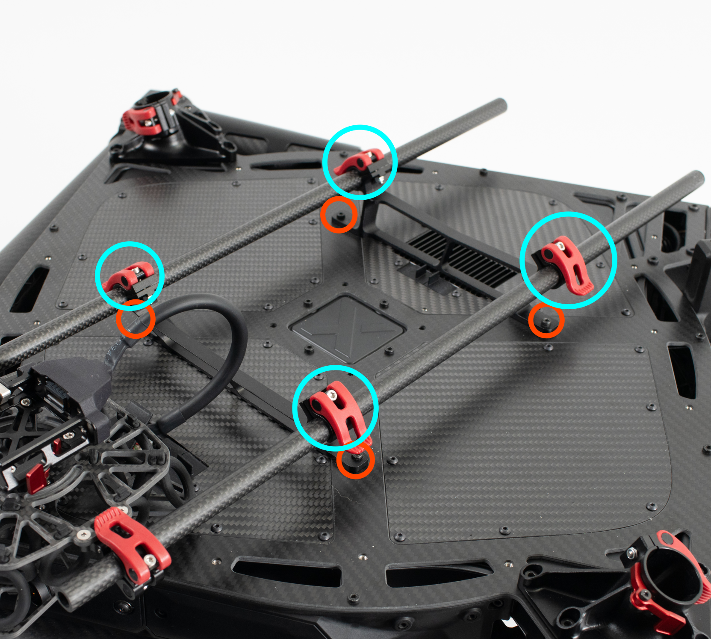
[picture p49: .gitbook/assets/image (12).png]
    <figure><figcaption></figcaption></figure>
5. Slide on or set the isolator on the rails. Close the locking levers loosely to retain the isolator on the rail.

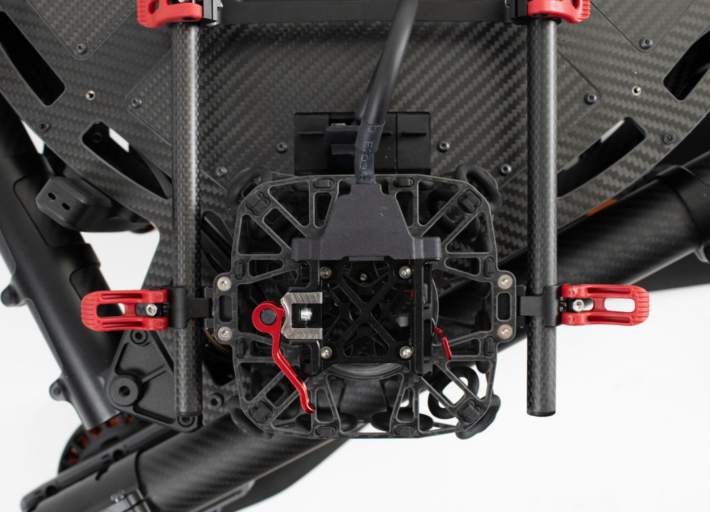
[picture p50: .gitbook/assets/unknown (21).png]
<figure><figcaption></figcaption></figure>

6. If you are using the default payload offset for Alta X Gen2, position the isolator with 110mm between the isolator and rail adapter clamps.
   1. This ensures the best accuracy when mapping. If you have adjusted this for your application, mount the isolator accordingly.

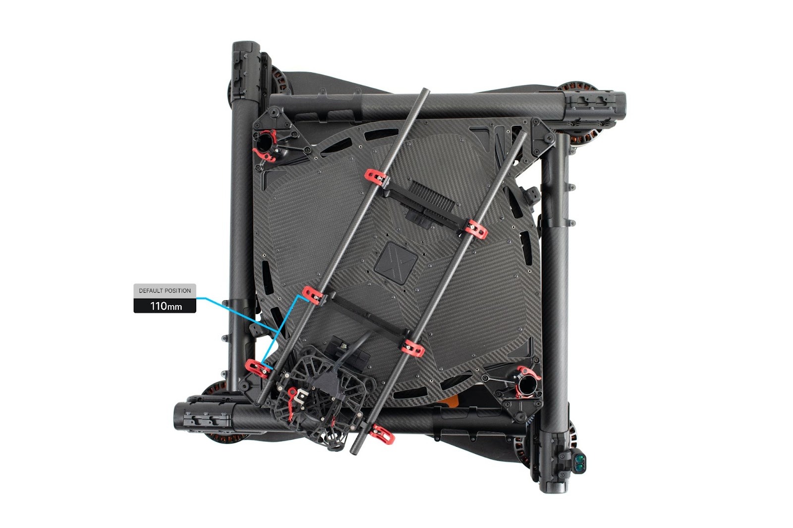
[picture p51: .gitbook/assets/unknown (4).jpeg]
<figure><figcaption></figcaption></figure>

7. When fully aligned, clamp the isolator fully onto the rails.

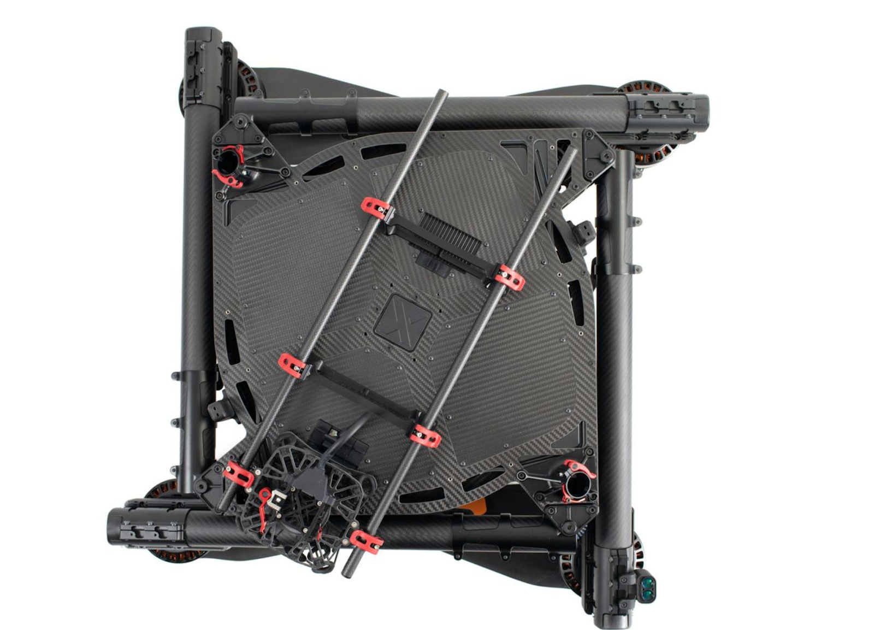
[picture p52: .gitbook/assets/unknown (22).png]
<figure><figcaption></figcaption></figure>

8. Plug in the Smart Dovetail cable into the Payload connector on the IO panel.

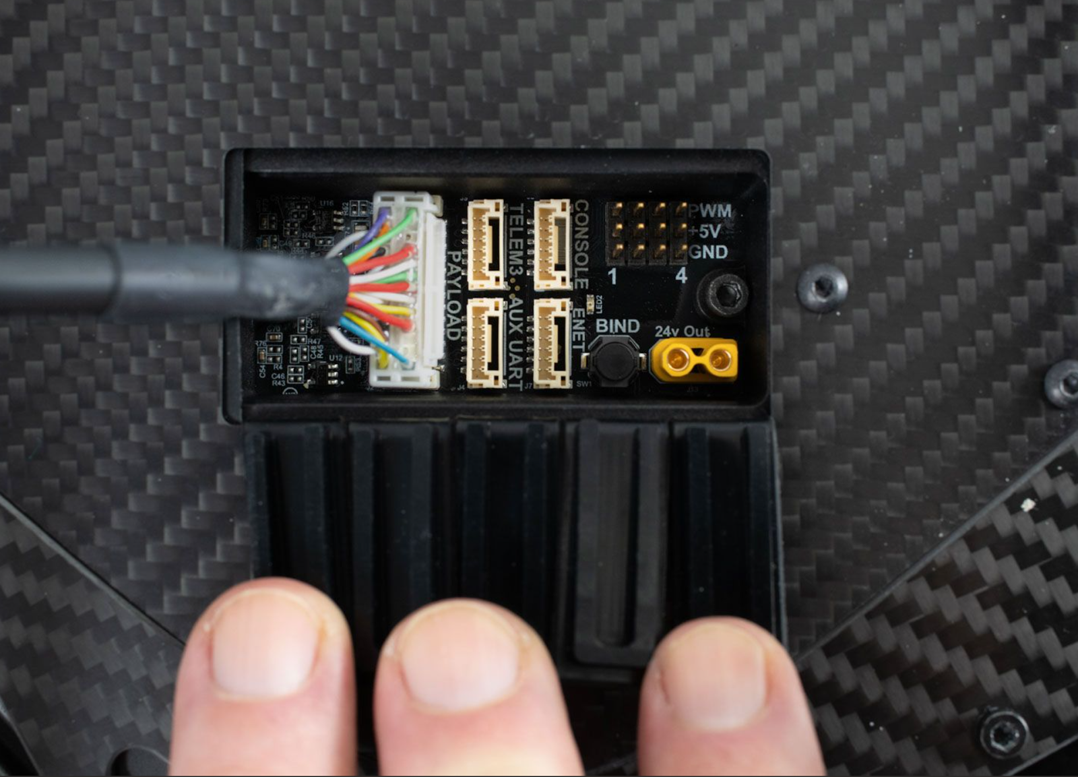
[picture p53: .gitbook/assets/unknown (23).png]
<figure><figcaption></figcaption></figure>

<br>

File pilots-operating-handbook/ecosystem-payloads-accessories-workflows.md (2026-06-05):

---
description: Where to go from here
hidden: true
---

# Ecosystem / Payloads / Accessories / Workflows

The [**Pilot's Operating Handbook**](https://app.gitbook.com/s/mvvtTxCd0o4luBB04PQp/pilots-operating-handbook) covers how to operate Alta X Gen2 itself: setup, flight modes, procedures, and emergencies.

**For everything else, see our Freefly Drone** [**Ecosystem Wiki**](https://app.gitbook.com/o/-LYU75KLzw4BcaiMGVz2/s/WXREyAKYAeQJ4gfg2SPg/)**. Payloads, accessories, workflow guides, and software integrations are shared resources that work across Freefly aircraft.**

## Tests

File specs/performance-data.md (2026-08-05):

---
icon: chart-mixed
---

# Performance Data

## Flight Time

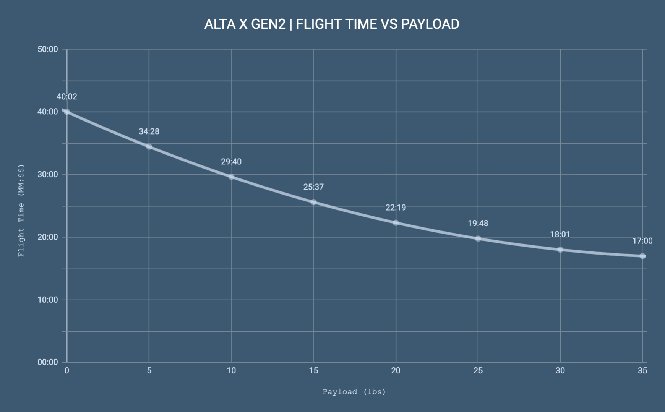
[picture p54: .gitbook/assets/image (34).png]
<figure><figcaption></figcaption></figure>

Our flight tests for the Alta X Gen2 were conducted by running the batteries from 100% down to 0%. While this is not typical in real-world operations—where a pilot would usually land with some remaining battery for safety—it provides a clear baseline for comparing performance between airframes and payloads. Furthermore, hovering draws more power than flying forward at a moderate speed. Because most real flights involve some forward motion (rather than continuous hovering), these 100%–0% hover results end up being a fair representation of typical flights that land with higher battery reserves.

***

## Thrust To Weight Ratio

***

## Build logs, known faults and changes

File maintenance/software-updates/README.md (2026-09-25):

---
icon: rotate
---

# Software Updates

{% hint style="warning" %}
**#protip** - Verify all Alta X Gen2 components have their software updated together to the latest by referencing the chart below to make sure there are no compatibility issues.
{% endhint %}

## Current Firmware Version

<a href="https://freeflyeng.s3.us-west-2.amazonaws.com/_SoftwareReleases/skynode-altaxgen2-v2.3.7-prod.auterionos" class="button primary">DOWNLOAD v2.3.7</a>

<details>

<summary><strong>Alta X Gen2 v2.3.7</strong></summary>

* **Summary**: Feature release bringing a Doodle radio firmware update, thermal mapping features, Pilot Pro RTK improvements, and more
* **Release Date**: September 2026
* **Versions in this package**:
  * Alta X Gen2 Skynode: v2.3.7
  * PX4: v2.3.6
  * AMC: 2.1.0
  * Pilot Pro App: 2.8.6
  * Freefly Updater App: 3.1.2
* **Notes** (Going from Alta X Gen2 v2.2.6 to v2.3.7)
  * **Read more about the highlights** [**here**](https://docs.freeflysystems.com/astro/maintenance/software-release-notes/astro-software-v2.3-whats-new)**.** Astro and Alta X Gen2 share the same v2.3 software release, so the same notes apply.
  * **Flight**
    * **New:** Boom LED feedback during radio pairing.
    * **New:** Pilot Pro kill switch link health check.
    * **New:** Enabled Dual-antenna GNSS heading.
    * **New:** Check for significant disagreement between magnetic and GNSS heading.
    * **New:** Warnings when either GPS module is missing.
    * **Fix:** More permissive in-air GPS checks no longer apply during pre-arm checks.
    * **Fix:** Gimbal tilt-rate zoom scaling no longer applies twice.
    * **Fix:** Drone can no longer initiate failsafe RTL after emergency flight termination.
    * **Fix:** In Manual mode, the arming stick gesture no longer pans the gimbal before takeoff.
    * **Fix:** Switching to automated takeoff immediately after arming in Manual mode no longer skips motor spoolup.
    * **Fix:** Yaw setpoint no longer shifts unexpectedly when switching from Position to Manual mode.
    * **Fix:** Drone no longer maintains vertical velocity too long after switching from Manual to Position mode.
  * **Payload**
    * **Boson Thermal Camera**
      * **New:** FLIR RJPEG image file format support.
      * **New:** Camera multi-capture for missions.
      * **Improvement:** Wildfire preset gamma updated to 1.6.
    * **LR1 Laser Range Finder**
      * **New:** Laser range finder driver installed by default.
        * Blue units can use the LRF add-on without breaking compliance by allowing app installation.
        * **Note:** Uninstall the previously installed `camera-distance-sensor` AOS app to avoid conflicts. See [here](https://docs.freeflysystems.com/ecosystem/payloads/lr1-payload/expansion-modules/lr1-laser-range-finder-module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) for instructions.
  * **Pilot Pro**
    * **New:** Added a setting to automatically reconnect to an RTK correction source at startup.
    * **Improvement:** Clearer RTK correction status UI.
    * **Improvement:** NTRIP server compatibility, including NTRIP 2.0 casters and chunked data transfer.
    * **New:** Save and load multiple NTRIP server profiles.
    * **New:** Tablet volume raises to 100% when armed and restores when disarmed. Configurable in **Tablet Settings**.
    * **Improvement:** Pilot Pro data interface now reports the active IO mapping configuration, verification status, parameter checksum, app version, and interface version.
    *   **Doodle Radio Firmware**

        * **New:** [Update Doodle radio firmware](https://app.gitbook.com/s/WXREyAKYAeQJ4gfg2SPg/controller/pilot-pro/operating-handbook/radio-modules/doodle-labs-radio-module/doodle-firmware-update) to version 2.0 through the Pilot Pro app.

        <div data-gb-custom-block data-tag="hint" data-style="warning" class="hint hint-warning"><p>Make sure to update the Drone to v2.3.7 before attempting to update the Doodle Radio Firmware.</p></div>

        * **Improvement:** Doodle 2.0 includes bug fixes and improved resilience in heavy RF interference.
  * **Auterion Mission Control**
    * **Improvement:** Base AMC version updated to 1.37.
    * **New:** “Mission Capture Camera” option for multi-camera capture during missions.
    * **Improvement:** Simplified version information in **Vehicle Overview** → **More**.
    * **Improvement:** Manual-mode hover throttle adjustment moved to **Vehicle Overview** → **Flight Config**. It is now shown in normal and advanced modes.
    * **Improvement:** System Health user experience:
      * Standardized vehicle status and health-check severity colors.
        * Red: arming is denied.
        * Orange: arm with caution.
      * **System Health** is now the default panel in **Vehicle Overview**.
      * Added inactive-mode health-check failures to the panel. These result in an orange caution status.
      * Improved several health-check messages.
      * Improved prioritization and deduplication of banner and audible alerts.
      * Disabled audible alerts while disarmed.
    * **New:** Download only new vehicle photos when viewing the gallery.
    * **New:** Button to stop pending downloads while viewing the gallery.
    * **New:** Thermal Next Palette button mapping in normal mode.
    * **New:** Toggle Map/Video button mapping to switch views in the Fly screen.
    * **Improvement:** Firmware compatibility check warns when vehicle firmware is below the minimum compatible version.
    * **New:** LR1 + Boson survey-planning preset.
    * **New:** Pre-filled filename when saving a mission loaded from file.
    * **Improvement:** Removed Acro mode from available flight modes in advanced mode.
    * **Fix:** Parameter files now save with a valid file extension.
    * **Fix:** Parameter files can now be found when loading.
    * **Fix:** All health-check failures are now shown.
    * **Fix:** Health-check failures are shown after failsafe landing from Position Slow mode.
    * **Fix:** Mission flight speed no longer resets when navigating from mission settings.
    * **Fix:** Map tiles now load on iPhone hotspots.
    * **Fix:** Mission flight-speed units now convert correctly.
    * **Fix:** Importing a mission plan now loads mission altitude correctly.
    * **Fix:** Rocker deadband adjustments now apply correctly.
    * **Fix:** The Plan screen is no longer blank after switching from Fly with the camera feed maximized.
    * **Fix:** “Missions do not require Takeoff Item” no longer blocks mission planning.
    * **Fix:** Long-pressing camera zoom buttons now continuously adjusts zoom.
    * **Fix:** The map now centers on the vehicle reliably when it has a GPS position.

</details>

### Latest Versions

<table data-full-width="true" data-search="false"><thead><tr><th width="221">Component</th><th width="248">Current Compatible Versions</th><th width="245">How To Update</th></tr></thead><tbody><tr><td><strong>Alta X Gen2</strong></td><td></td><td></td></tr><tr><td>Software</td><td>2.3.7</td><td><a href="updating-firmware.md#updating-alta-x-gen2-firmware">Alta X Gen2 Firmware</a></td></tr><tr><td><strong>Pilot Pro</strong></td><td></td><td></td></tr><tr><td>Pilot Pro Firmware</td><td>2.2.0</td><td><a href="https://docs.freeflysystems.com/ecosystem/controller/pilot-pro/maintenance/software-and-firmware-updates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">Update</a> through the Pilot Pro App</td></tr><tr><td>Pilot Pro App</td><td>2.8.6</td><td>Check the <a href="https://docs.freeflysystems.com/ecosystem/controller/pilot-pro/maintenance/software-and-firmware-updates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">"updates"</a> section in Updater app</td></tr><tr><td>Doodle Radio Firmware</td><td>2.0</td><td>Check the "<a href="https://app.gitbook.com/s/WXREyAKYAeQJ4gfg2SPg/controller/pilot-pro/operating-handbook/radio-modules/doodle-labs-radio-module/doodle-firmware-update">Radio Settings -> Radio Firmware</a>" section in Pilot Pro App</td></tr><tr><td>AMC App</td><td>2.1.0</td><td><p>Check the <a href="https://docs.freeflysystems.com/ecosystem/controller/pilot-pro/maintenance/software-and-firmware-updates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">"updates"</a> section in Updater app.</p><p><strong>Desktop downloads:</strong></p><p><a href="https://freeflyeng.s3.us-west-2.amazonaws.com/_SoftwareReleases/AuterionMissionControl-amc-v1.37.25-freefly-astro-2.1.0-arm64.dmg">macOS (Apple Silicon)</a></p><p><a href="https://freeflyeng.s3.us-west-2.amazonaws.com/_SoftwareReleases/AuterionMissionControl-amc-v1.37.25-freefly-astro-2.1.0.exe">Windows</a></p><p><a href="https://freeflyeng.s3.us-west-2.amazonaws.com/_SoftwareReleases/AuterionMissionControl-amc-v1.37.25-freefly-astro-2.1.0-ubuntu.AppImage">Linux</a></p></td></tr><tr><td>Freefly Updater App</td><td>3.1.2</td><td>Check the <a href="https://docs.freeflysystems.com/ecosystem/controller/pilot-pro/maintenance/software-and-firmware-updates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">"updates"</a> section in Updater app</td></tr><tr><td><strong>Desktop Apps</strong></td><td></td><td></td></tr><tr><td>Freefly PPK App</td><td>1.2.2</td><td><a href="https://docs.freeflysystems.com/ecosystem/workflows/photogrammetry-mapping/ppk-software">Download</a> from the PPK Software page</td></tr><tr><td><strong>Payloads</strong></td><td></td><td></td></tr><tr><td>Freefly Payloads (LR1, A7R4, OGI, Wiris Pro)</td><td><a href="https://docs.freeflysystems.com/ecosystem/payloads/payload-maintenance/gimbal-firmware">See payloads page</a></td><td><a href="https://docs.freeflysystems.com/ecosystem/payloads/payload-maintenance/gimbal-firmware">Gimbal Firmware</a></td></tr></tbody></table>

***

## Previous Firmware Versions

### Alta X Gen2 v2.2 Release Notes

<details>

<summary><strong>Alta X Gen2 v2.2.6</strong></summary>

<a href="https://freeflyeng.s3.us-west-2.amazonaws.com/_SoftwareReleases/skynode-altaxgen2-v2.2.6-prod.auterionos" class="button primary">DOWNLOAD v2.2.6</a>

* **Summary**: New Feature Release. Brings new Boson thermal presets, LR1 and A7R photography improvements, Gremsy VIO plug-and-play, RTK/NTRIP from Pilot Pro, and the rewritten Doodle channel scan.
* **Release Date**: April 2026
* **Versions in this package**:
  * Alta X Gen2 Skynode: v2.2.6
  * AMC: 1.36.24
  * Pilot Pro App: v2.7
  * Gimbal Firmware: v2.3.0
  * Freefly Updater: v3.1.1
  * LR1 Camera Firmware (recommended): v3.0
* **Notes** (Going from Alta X Gen2 v2.1.x to v2.2.6)
  * **Read more about the highlights** [**here**](https://docs.freeflysystems.com/astro/maintenance/software-release-notes/astro-software-v2.2-whats-new)**.** Astro and Alta X Gen2 share the same v2.2 software release, so the same notes apply.
  * **Flight**
    * **Fix:** Strong magnetic interference warning wording updated for clarity.
  * **Payload**
    * **New:** LR1 and A7R Fixed Focus mode. Locks the camera at the current focus distance without re-racking, ideal after tap-to-focus for near subjects.
    * **Fix:** Blurry Infinity Focus on certain Sigma 24mm lens versions (v.03 firmware). The payload driver now reads lens firmware version and applies the correct focus offset per version, on both LR1 and A7R.
    * **New:** LR1 and A7R RAW and RAW+JPEG image format support. RAW images save to the camera SD card only.
    * **New:** Gremsy VIO is now plug-and-play. Swapping between an LR1 and a VIO no longer requires parameter changes. VIO must be configured correctly or purchased from Freefly. If using VIO geotagging, the MAVLink mode must be changed, which removes the blue configuration of the aircraft.
    * **New:** Boson Wildfire Contrast Preset, pre-configured for wildfire detection with advanced contrast and isotherm defaults.
    * **New:** Simplified Isotherm views for Boson. "Temp Above" and "Temp Below" each expose a single isotherm band, making it easier to highlight the hottest or coldest objects.
    * **New:** Advanced Contrast Settings for Boson are now in a separate dropdown. Switching Contrast Preset resets Advanced Contrast Settings to the new preset's values.
    * **Fix:** Boson radiometric TIFF captures are now significantly faster.
    * **Fix (AMC):** Flir Boson+ 640 added to available camera profiles.
    * **New:** LR1 APS-C crop support in video mode. Requires LR1 camera firmware newer than v1.0.0.
    * **New:** LR1 additional video recording formats, including XAVC S-I 4K.
    * **Fix (AMC):** Flux survey planning improvements.
  * **Pilot Pro**
    * **New:** RTK and NTRIP can now be run from Pilot Pro on MAVLink-over-ethernet vehicles.
    * **New:** Doodle radio channel scan now scores channels by airtime activity, not just noise, with visual bars and per-channel diagnostics.
    * **New:** Customizable Pilot Pro Status page for integrators.
    * **New:** Pilot Pro now always verifies all input-output parameters to ensure the applied config matches controller state.
    * **Improvement:** Android battery optimization configured so critical Freefly apps are not killed when backgrounded.
    * **Improvement:** Graceful tablet shutdown so Android settings persist across boot.
    * **Improvement:** Software update UX.
    * **Improvement:** Better vehicle and serial connection state management.
    * **Fix:** Log pruning is now capped at 3 GB.
    * **Fix (Freefly Updater):** Auto-fetch on app start now works reliably.
    * **New (Freefly Updater):** Pop-up warning when there is no internet connectivity.

</details>

### Alta X Gen2 v2.1 Release Notes

<details>

<summary>Alta X Gen2 v2.1.44</summary>

* **Summary**: First public release of Alta X Gen2 software.
* **Release Date**: January 2026
* **Versions in this package**:
  * Alta X Gen2 Skynode: v2.1.44

</details>

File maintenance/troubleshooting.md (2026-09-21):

---
icon: circle-question
---

# FAQ & Troubleshooting

## Troubleshooting

### Only one battery detected

If you have two batteries connected to Alta X Gen2 but are only seeing one battery in AMC:

* Check that both batteries are on. If one of the batteries doesn't have any LEDs lit up, try pressing the button on the battery to wake it.
* Verify that you are in smart battery mode. See the [Battery page](../other-user-manuals/ecosystem/batteries-and-charging.md#switching-battery-modes) for instructions on changing battery mode.
  * Dual battery display in AMC is only supported when smart battery mode is enabled.

### LTE not connecting

If you’re having trouble with LTE connectivity, here’s a few things to check:

* With Alta X Gen2 powered on and connected to AMC via Pilot Pro or a computer, check the LTE status in the dropdown.
* Ensure you’ve installed the SIM card properly.
* Check the APN and roaming settings under the Vehicle Overview -> Connectivity -> LTE menu in AMC.
* If you’re in an area with spotty coverage, try moving outside and away from large buildings.

### WiFi not connecting

* With Alta X Gen2 powered on and connected to AMC via Pilot Pro or a computer, check the WiFi status in the vehicle connectivity -> Connectivity -> Wi-Fi menu.
* Verify in the Wi-Fi tab that the button is on.
* Press the scan icon to search for network.
* Try moving Alta X Gen2 closer to the router or access point.
* Note that when RemoteID is enabled, WiFi's mode switches to serve RemoteID. It is a manual process for the pilot to switch the WiFi's mode to internet connectivity when not flying.

{% hint style="info" %}
5.8GHz WiFi networks have better performance due to less radio interference from the onboard RF
{% endhint %}

### Pilot Pro not connecting (rebind controller)

**For Alta X Gen2 with Herelink radio:**

* Prepare tweezers or paperclip.
* Power on Alta X Gen2 with one battery and the fused cable.
* Turn on Pilot Pro.
*   Wait 30 seconds for the drone to power on, then press the pairing button on the IO panel five times quickly. (The IO panel is located on the bottom side of the aircraft near the nose).

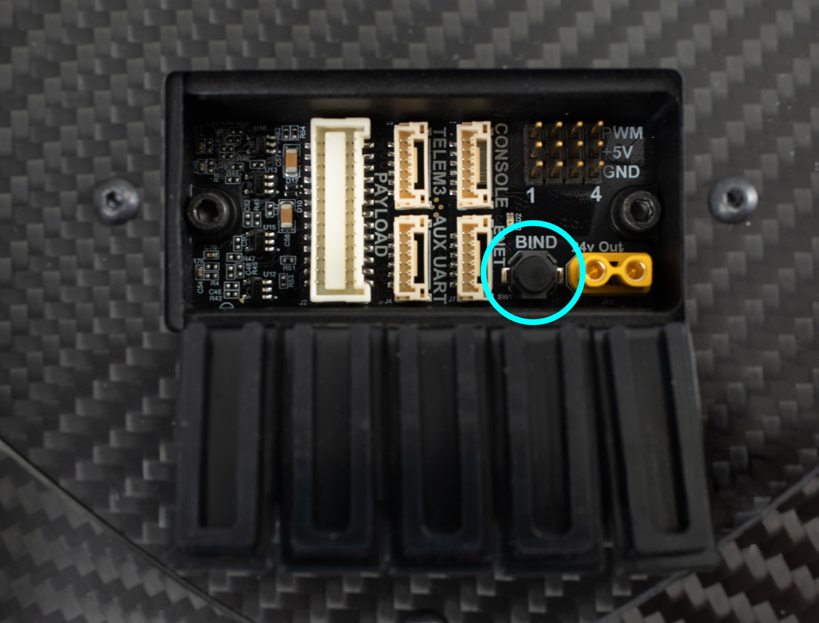
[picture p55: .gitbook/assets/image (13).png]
    <figure><figcaption></figcaption></figure>
* On the Pilot Pro side, locate the pairing button on the Herelink radio. Using tweezers, press and hold the Herelink Air Unit's "Pair/Reset" button until LED blinks (hold approximately 3 seconds).

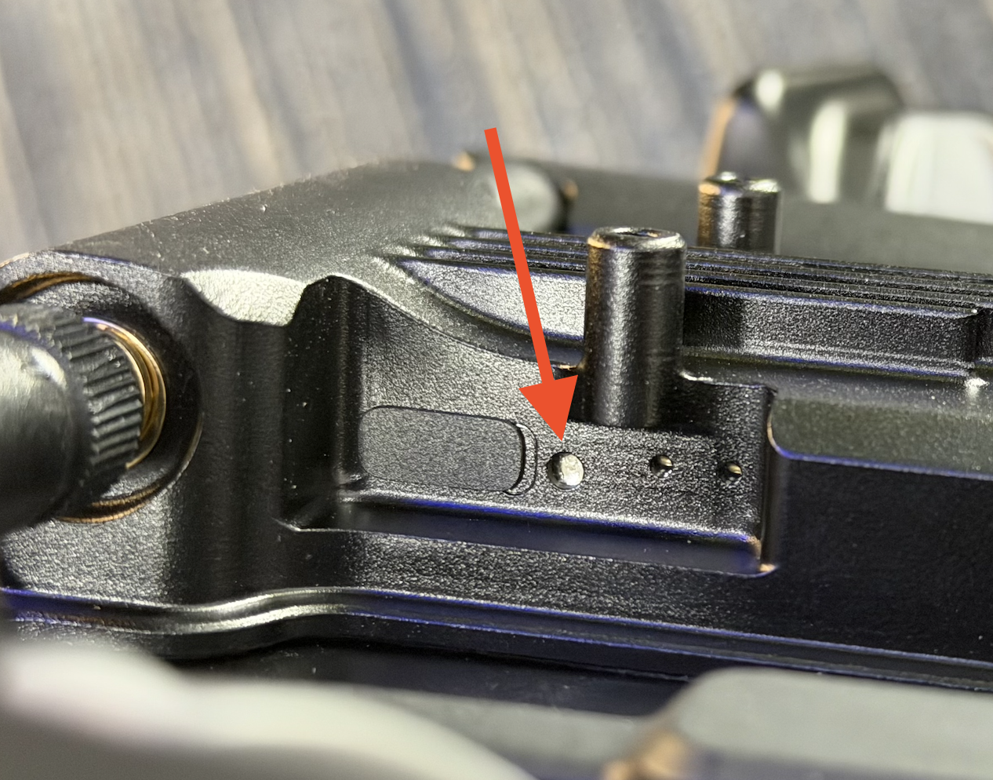
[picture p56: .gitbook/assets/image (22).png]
<figure><figcaption></figcaption></figure>

* Wait for Pilot Pro and Alta X Gen2 to pair. Once paired, Pilot Pro's power button LED should turn green.

**For Alta X Gen2 with Doodle Labs radio:**

* Make sure Alta X Gen2 and Pilot Pro are at least 6-10’ apart. The Doodle Labs radios are powerful and may interfere with each other at close range.
* Power on Alta X Gen2 with one battery and the fused cable.
* Power on Pilot Pro.
* Give it time. Each radio takes about 60 seconds from power-up to fully boot its system. Ensure both the air and ground radios have been powered on for at least 60 seconds before checking connectivity.
* Open the Pilot Pro App and open the side menu. Navigate to "Radio Settings". Then open "Pairing Manager".

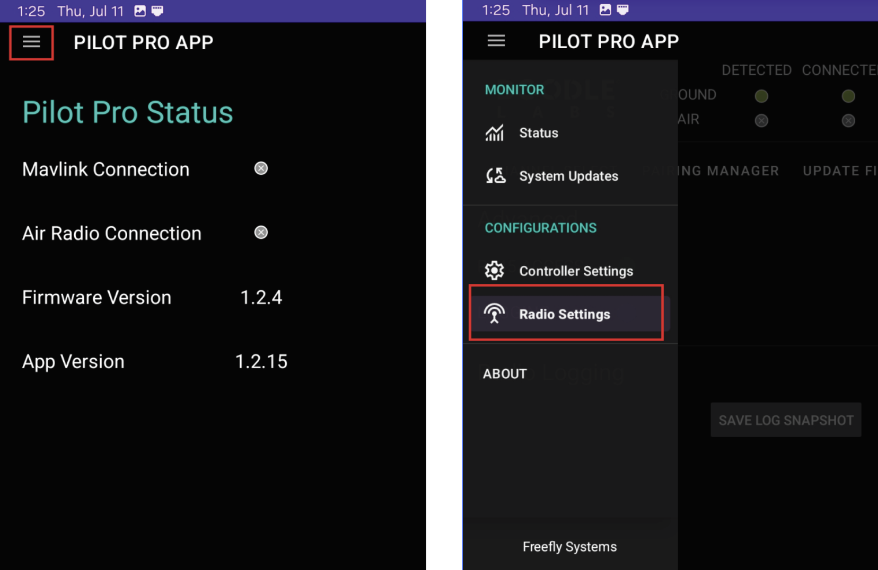
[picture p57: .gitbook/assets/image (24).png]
<figure><figcaption></figcaption></figure>

*   Locate and press the binding button on the IO panel five times quickly. (The IO panel is located on the bottom side of the aircraft near the nose).

    <figure><figcaption></figcaption></figure>
* Wait for 30 seconds for the radio to go into pairing mode, then press “Scan” on Pilot Pro App.
* From the list of results, find the one that matches Alta X Gen2's serial number. Then press pair.
* Wait 60 seconds for process to complete.

## FAQ

#### Does Alta X Gen2 have dual GNSS heading?

* Alta X Gen2 ships with dual onboard F9P GNSS receivers. This currently enables redundancy in case of a single module failure. A future software update will enable dual GNSS aided heading estimation for better performance in degraded conditions.

<br>

#### Does Alta X Gen2 support terrain following?

* Auterion Mission Control has [Digital Elevation/Terrain Model (DEM)](https://www.earthdata.nasa.gov/topics/land-surface/digital-elevation-terrain-model-dem) built into its mission planning features that allow Alta X Gen2 to utilize terrain following during missions.
* Alta X Gen2 also includes sensors (laser range finder) to support terrain following, but it is not currently supported in software. We plan to include support for it in a future release.

<br>

#### What power is available onboard?

* Alta X Gen2 includes connectors for unregulated battery power, and regulated 12V and 24V power.
* Accessory battery power is fused at 10A.
* 12V power is limited to 10A (120W).
* 24V power is limited to 6.25A (150W).

<br>

#### Can I use other batteries with Alta X Gen2?

* Yes, but this requires parameter changes. Alta X Gen2 is designed to use the recommended smart batteries, as these are the most heavily tested and they enable more accurate battery state of charge measurement, but it can be configured to operate on other batteries.
* Note: changing battery modes disables single battery arming prevention. Always use a fused power cable with one battery when powering the aircraft on the ground or bench.
* To use XT90 batteries with Alta X Gen2, we offer adapter cables. Contact [Support](https://freeflysystems.com/support) to purchase these.
* To change battery modes, see [here](../other-user-manuals/ecosystem/batteries-and-charging.md#switching-battery-modes).

<br>

#### Does Alta X Gen2 include an FPV camera?

* Yes, all variants of Alta X Gen2 include a forward facing NDAA compliant digital FPV camera that streams into AMC on Pilot Pro.

<br>

#### Can I use multiple Smart Dovetail payloads?

* Skynode on Alta X Gen2 only supports interfacing to one Smart Dovetail payload at a time. Alta X Gen2 can support multiple payloads if only one is using the Smart Dovetail interface and the others are passive or power only.

<br>

#### What’s the max flight time?

* Alta X Gen2’s flight time depends on payload and density altitude. See the performance chart here.

<br>

#### What payloads are supported on Alta X Gen2?

* Alta X Gen2 supports the same payloads as Alta X Gen1, in addition to the following Smart Dovetail payloads. We continue to test new payloads and expand the list of supported payloads.
* LR1 Payload
* Gremsy Vio Payload
* Movi Pro / Carbon
* Flux Payload integration is in the works

#### How can I get help?

* Reach out to support by emailing us at support@freeflysystems.com or via our [website](https://freeflysystems.com/contact). Texting or sending social messages will take longer.
*   Share as much detail as possible and provide Alta X Gen2's serial number (located on the rear end of the aircraft by the battery connectors).

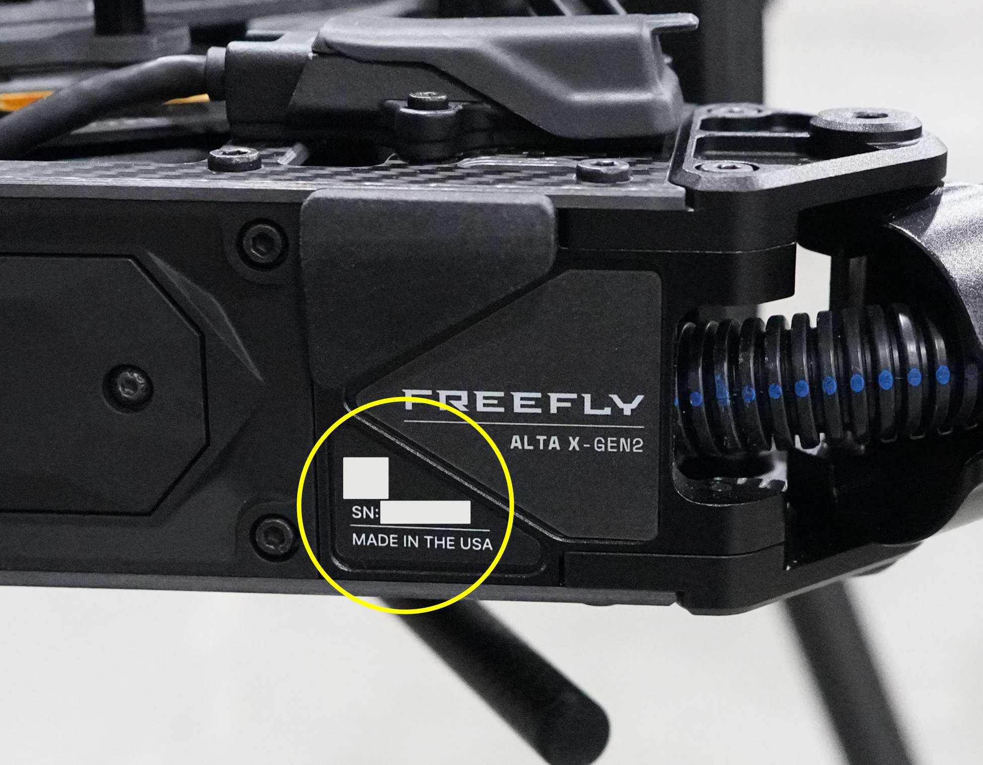
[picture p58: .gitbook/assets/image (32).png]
    <figure><figcaption></figcaption></figure>
* Share your flight logs from the Auterion Suite.
* Include photos or videos in your contact in order to get us up to speed as quickly as possible.
* Include pilot statement and notes of any incident or details

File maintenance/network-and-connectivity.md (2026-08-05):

---
icon: circle-wifi
---

# Network and Connectivity

### WiFi

This section describes the connection process for Alta X Gen2's built-in WiFi radio. This functionality is useful while the aircraft is on the ground, for admin and setup tasks. Connecting the Alta X Gen2 to wifi is required to complete the initial [Auterion Suite setup process](https://freefly.gitbook.io/astro-public/pilots-operating-handbook/essential-software/auterion-suite).

#### Connect the Alta X Gen2 aircraft to a wifi network

{% tabs %}
{% tab title="Video" %}
{% embed url="https://www.loom.com/share/b81f0678863947c192e09fe474aee709" %}
{% endtab %}

{% tab title="Text" %}
1. Open AMC GCU or PC. If using a PC, connect to Alta X Gen2 with a USB-C cable.
2. Tap on the vehicle status button at the top of the AMC screen (it will be either red, yellow, or green depending on the vehicle's status).
3. Select Connectivity.
4. Enable Wifi and disable Hotspot Mode.
5. Scan for the network then click on it and enter the password, then connect.
{% endtab %}
{% endtabs %}

{% hint style="info" %}
Alta X Gen2's WiFi module is compatible with 5.8GHz and 2.4GHz bands. When possible, use 5.8GHz for better throughput and performance.
{% endhint %}

#### Connect to the Alta X Gen2 hotspot via WiFi

1. Open AMC on Pilot Pro or via a computer. If using a PC, connect to Astro with a USB-C cable.
2. Power Alta X Gen2.
3. Tap the icon in the top-left of AMC. Navigate to Vehicle Setup > WiFi.
4. Set Wifi Mode to Hotspot, which allows Alta X Gen2 to broadcast a WiFi network that other devices can connect to.

***

### LTE

If your Alta X Gen2 has an LTE sim card installed, you can utilize online features such as live video, real-time aircraft status, and flight logs through [Auterion Suite](https://freefly.gitbook.io/astro-public/pilots-operating-handbook/essential-software/auterion-suite).

{% hint style="warning" %}
Currently, Alta X Gen2 is only available with an LTE radio suitable for North American markets. Additional LTE compatibility will be available in the future.
{% endhint %}

#### Configure and Enable / Disable

1. [Install a SIM card](standard-maintenance-procedures.md#installing-a-sim-card) into Alta X Gen2. Make sure to write down the SIM card number found on the card if you don't have it recorded elsewhere.
2. Open AMC on Pilot Pro or a connected PC
3. Navigate to Vehicle Setup > Cellular
4. If you need to access the IMEI number for the vehicle to enable the SIM card, connect to the Alta X Gen2 with a PC and USB-C cable
   1. Power on Alta X Gen2 with one battery and the fused cable only.
   2. Using a web browser, navigate to [http://10.41.1.1/](http://10.41.1.1/) then click "System Status" in the sidebar.
   3.  Scroll until you find the listed IMEI information<br>

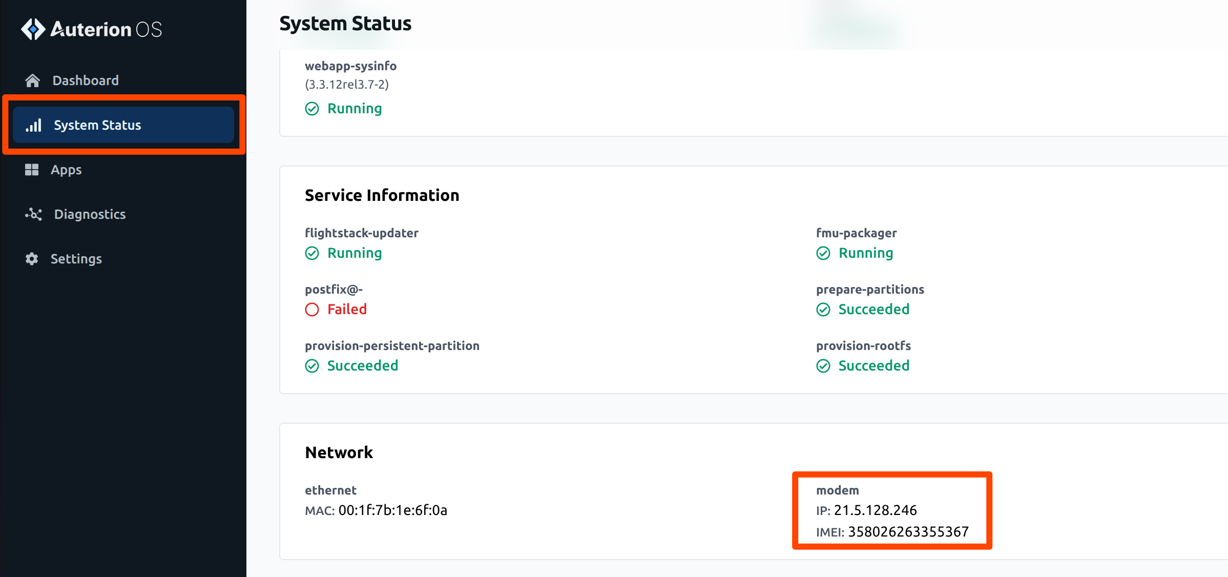
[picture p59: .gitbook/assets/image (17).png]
       <figure><figcaption></figcaption></figure>

#### Hardware Disable

You can assure that LTE is not being used by [removing the SIM ](https://freefly.gitbook.io/astro-public/astro/maintenance-manual/replacing-components/installing-a-sim-card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)card from Alta X Gen2.

#### Frequencies and Compatibility

| Region | 4G LTE Bands | Radio Spec Sheet |
| --- | --- | --- |
| North America  | B2, B4, B5, B13, B17 | [https://www.sierrawireless.com/products-and-solutions/embedded-solutions/products/hl7588-accessory-board/](https://www.sierrawireless.com/products-and-solutions/embedded-solutions/products/hl7588-accessory-board/) |
| EMEA/Australia | Cat-4: B1, B3, B7, B8, B20, B28 | [https://www.sierrawireless.com/products-and-solutions/embedded-solutions/products/rc7620/](https://www.sierrawireless.com/products-and-solutions/embedded-solutions/products/rc7620/) |

{% hint style="warning" %}
Currently, Alta X Gen2 is only available with an LTE radio suitable for North American markets. Additional LTE compatibility will be available in the future.
{% endhint %}

#### Changing SIM / Service Provider

When switching SIM cards, try leaving the APN field blank. It should be automatically detected. If not, here are a few suggestions.

| Carrier  | APN |
| --- | --- |
| T-mobile | iot.tmowholesale, fast.t-mobile.com |
| Orange | orange.m2m.spec |
| Verizon  | See: [https://www.verizon.com/support/knowledge-base-46578/](https://www.verizon.com/support/knowledge-base-46578/) |

In most cases, check the "Allow Roaming" box.

After changing the SIM, reboot both the aircraft and AMC.

***

### Installing a SIM card

Alta X Gen2 has an onboard North American LTE modem for remote connectivity. To install a SIM card:

1.  Place Alta X Gen2 upside down on a clean flat surface with the nose pointing away from you.

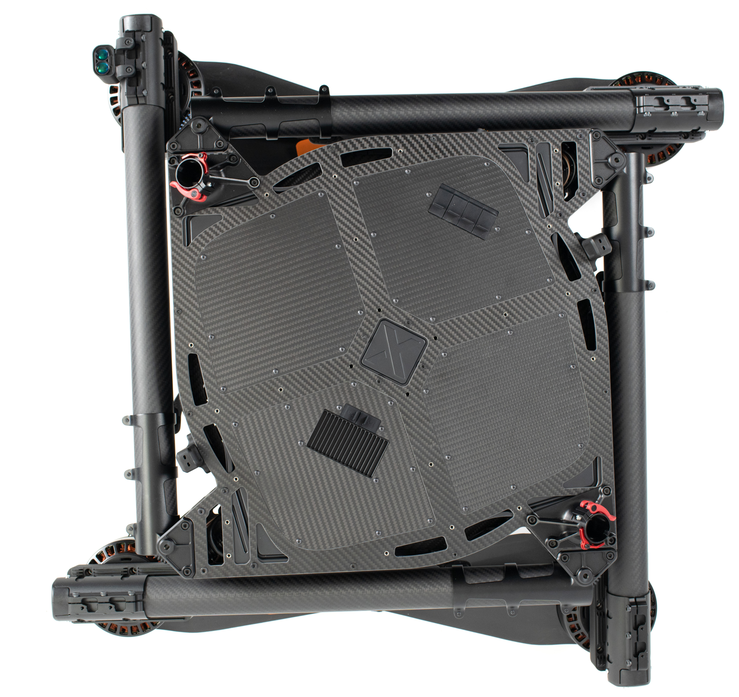
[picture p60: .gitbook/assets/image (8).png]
    <figure><figcaption></figcaption></figure>
2.  Using the included 2mm hex driver, remove the 9 screws from the bay door on the left side of the aircraft.

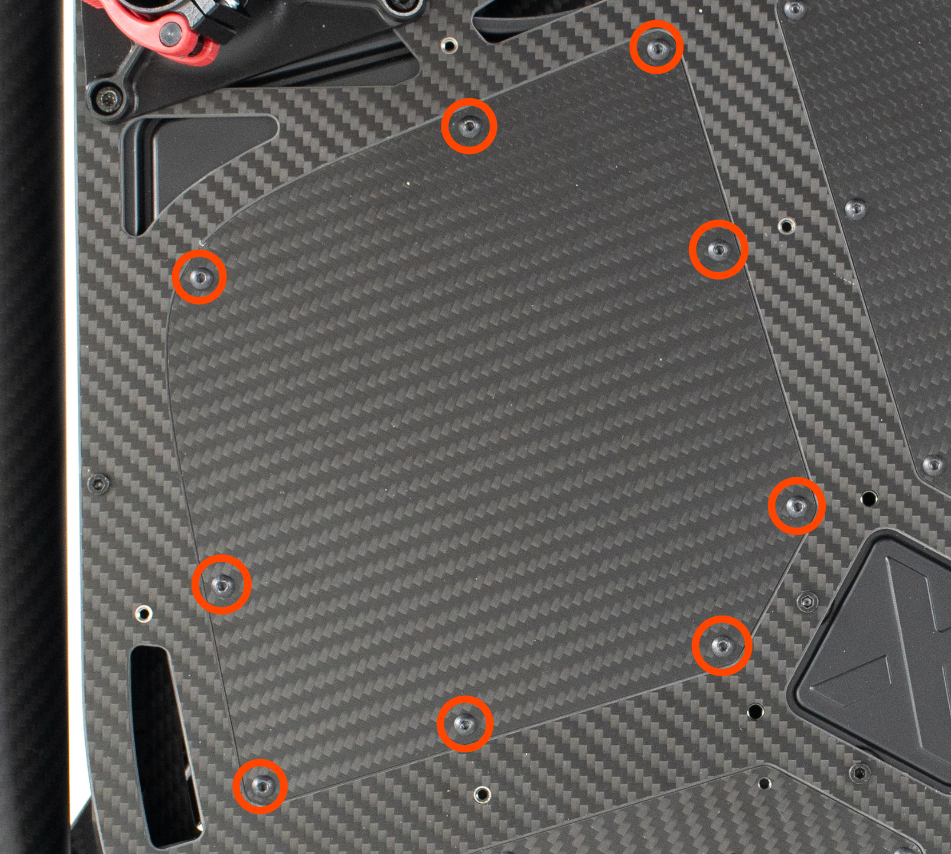
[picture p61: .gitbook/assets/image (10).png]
    <figure><figcaption></figcaption></figure>
3.  Remove the carbon fiber panel.

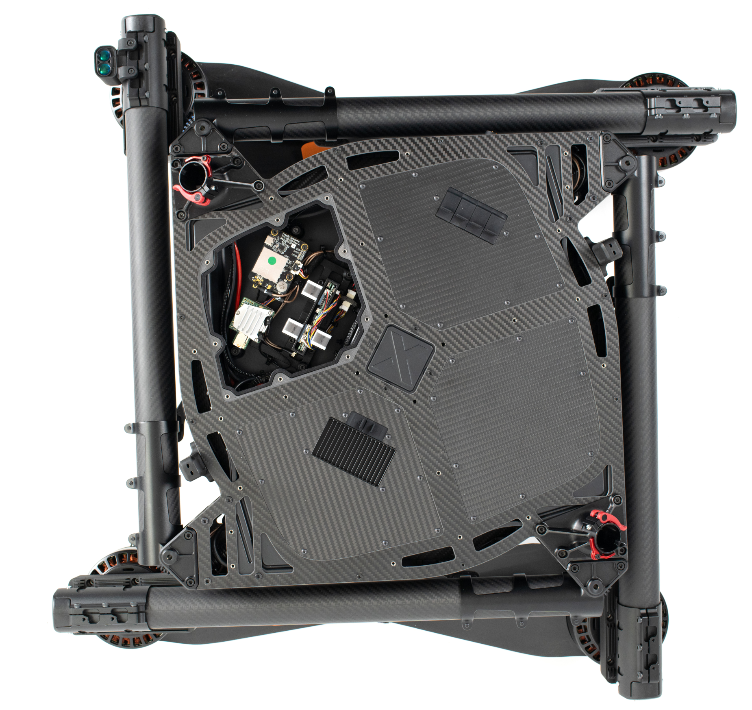
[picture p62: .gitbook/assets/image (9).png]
    <figure><figcaption></figcaption></figure>
4.  Insert the SIM card into the SIM card slot on the LTE modem. Ensure the card is fully seated and clicks in.

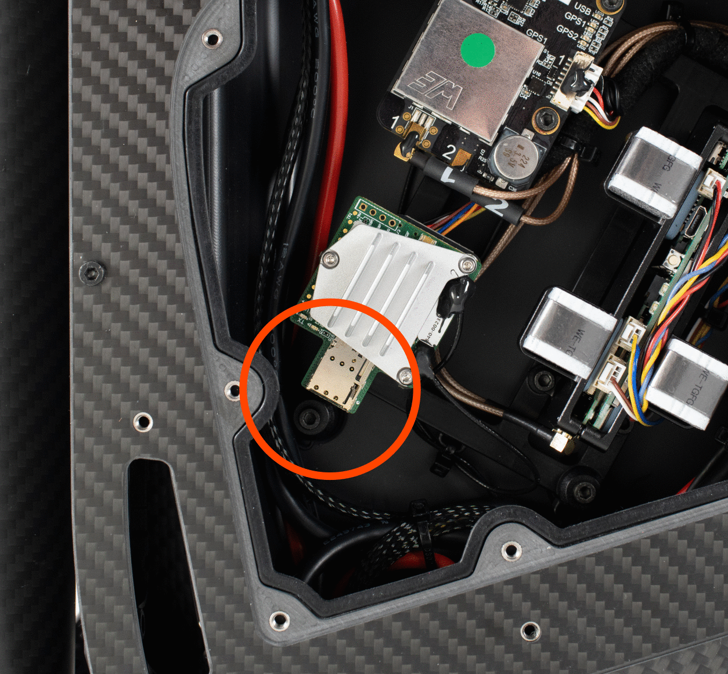
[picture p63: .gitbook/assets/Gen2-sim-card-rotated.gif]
    <figure><figcaption></figcaption></figure>
5.  Reinstall the carbon fiber panel and loosely screw in all 9 screws holding the panel in place.

    <figure><figcaption></figcaption></figure>
6. Once all screws are installed, hand tighten all screws, working in a star pattern around the panel.
7. Power on Pilot Pro.
8. Power on Alta X Gen2 with one battery and the fused cable.
9. Open AMC on Pilot Pro, click vehicle overview, select connectivity, then LTE.
10. Enter the APN for the cellular service provider in the box, then click save.
11. Verify the cellular status shows connected.

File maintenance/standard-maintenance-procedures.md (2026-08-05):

---
icon: wrench
---

# Standard Maintenance Procedures

{% hint style="danger" %}
Before performing any maintenance, ensure that Alta X Gen2 has been unplugged from any power source. Leaving Alta X Gen2 powered while performing any work on it can result in a potentially dangerous situation.
{% endhint %}

#### Cleaning 

Keep your aircraft clean of dust and debris after each use. This will ensure that moving parts are not damaged/worn/jammed and also helps prevent contamination from hiding structural damage that must be identified during visual preflight inspections.

Clean Alta X Gen2's exterior with a non-abrasive soft cloth, microfiber towel or similar with a plastic-safe soap or detergent. Graduate the solvent potency when removing contamination, as shown below:

1. Water
2. Soap and water
3. General cleaner (like Simple Green)
4. Isopropyl Alcohol

Avoid anything that has bleach in it, or aggressive solvents like Acetone. If operating in a salt environment, wipe down Alta X Gen2 after use with a clean rag wet with tap water.

## Preventative Maintenance Schedule

Always follow the preflight checklist items to ensure that each flight is safe and achieves the mission goals.

If an item is not specifically listed under any preventative maintenance schedule below, then the item is rated for the lifetime of the aircraft. This does include all aircraft electronics and motors.

At any point if you are concerned about something on the aircraft you can contact Freefly Support or purchase a Preventative Maintenance Checkup.

{% hint style="warning" %}
Note: it is key to keep both your aircraft and controller firmware up to date. Review the [Software Release Notes](https://github.com/freefly-systems/wiki-public-alta-x-gen2/blob/main/maintenance/software-updates.md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) or review the software updates page in the Auterion Suite to maintain your vehicle firmware.
{% endhint %}

### Every Flight

* Perform a full visual inspection of the drone, controller, batteries, and payloads before each flight.
* Look for any missing screws or hardware, any new damage or cracks, or anything that looks out of the ordinary or has changed.
* Check that motors spin freely and with no grinding/interference.
* Check that the propellers move freely and that the ActiveBlade dampers are in place.
* Developing this mental model of your drone is key to catching issues before they become a possible in-flight emergency.

### Every 15 Flight Hours

**Perform a detailed visual inspection of the aircraft:**

* Propeller blades and fasteners
  * Motor mounting fasteners are present and not loose.
  * Propeller blades are flight ready. Reject if chips, cracks, or deep scratches are visible. Replace as necessary with spare parts.
  * ActiveBlade dampers are present and intact.
* Boom ring latch
  * Check boom latching tightness by closing the latch. There should be a firm closing force and click. Adjust the tension by using a 2.0mm hex wrench on the set screw located in the rear of the latch link.
* Inspect Landing Gear
  * Look for: Loose latches, debris, any visible cracks or damage.
* Vibration Isolator
  * Visually check for any stretching, detached o-rings, or damage. Replace as necessary with spare parts.

**Clean aircraft**

* Wipe down any dust/debris from chassis
* Clean any contamination from battery connectors
* Ensure no debris in or around the boom motors
* Clean off any debris on propellers

### Every 3 months

For long-term storage, it is recommended you put your batteries on a storage charge every 3 months. The batteries can over discharge over time due to parasitic loss in the BMS. Making sure your batteries are at proper storage voltage every three months will prevent permanent damage due to over-discharging.

The longevity and health of the battery is fully dependent on how you treat and care for it. One important aspect of the care of a LiPo is storage voltage. Storing the battery at a charged voltage for more than 2-3 days will start to degrade the battery. The optimal storage voltage for lipos is 3.8v to 3.9v per cell (45.6v to 46.8v total.) After a mission, a Lipo charger can be used to put batteries in “Storage Mode”. This will either discharge or charge your battery to get it to storage voltage. Batteries should be placed in a cool environment with a recommended storage temperature from 10°C to 25°C. For storage make sure your battery is kept in a dry fireproof cabinet.

### Every 250 Flight Hours

**Inspect all fastener locations to verify fasteners are present, not damaged, and are not loose.**

Check the tightness of the following fasteners to verify no loose fasteners or use a torque stripe/seal to ensure bolts have not moved.

To check fasteners, apply a slight tightening torque (Clockwise direction) to each fastener on the chassis using the supplied hex drivers. The fasteners should not slip. Do not try to tighten the fastener, only check if it is loose

If a fastener does slip, tighten it using the methods described in the "Fastener Installation" section below. Do not apply additional thread locking compound unless the fastener has repeatedly come loose.

#### Items that need tightness verified (ensure they have not worked loose):

* Motor mount bolts (attaches motor mount to boom)
* Propeller mount bolts (attaches props to motor)
* Prop tension
* Top and bottom chassis bolts
* Payload Isolation Mount
* GPS antenna tightness
* Antenna mast bolts
* Landing gear bolts
* Any payload fasteners

### PM4: Every 750 Flight Hours

* Freefly recommends to perform this maintenance every year even if the aircraft has not hit 750 flight hours, especially if the aircraft has missed other PM intervals or if the drone operates in harsh or abusive conditions
* Send Alta X Gen2 in for a Freefly Service Inspection and Overhaul
  * Freefly drone service team will perform a full visual inspection and functional test of your aircraft with specific emphasis on:
    * Wear/fatigue items
    * Updated/improved/revised components
    * Confirm performance thresholds
      * Motors
      * Sensors
      * Any payload stabilization metrics
    * The service will include:
      * Historical flight log review for any errors or trends that need to be addressed (shared via Auterion Suite)
      * Service bulletin and firmware updates
      * Full airworthiness inspection
      * Full cleaning and fastener replacement (as needed)
      * System level test and re-qualification

## What to do if an Inspection Fails?

First step is to evaluate if the problem can be fixed. Things that can be fixed by the user typically are:

* Dirty or contaminated hardware
* Loose fasteners (Ensure you have the correct type of Loctite threadlocker)
* Missing fasteners (If you have the correct replacement parts)
* Any replacement parts that you bought from the store or have specific directions from Freefly Customer Support

If you have a failure and cannot fix using our general guidelines or the spare parts provided in the kit or on the store, please reach out to support@freeflysystems.com or [submit a direct ticket](https://freeflysystems.com/contact) for any questions, specific replacement needs or issues! We are here to help you get safely and quickly back into the air!

If you need to purchase spare or replacement parts, please go to [store.freeflysystems.com](http://store.freeflysystems.com) to purchase our standard parts.

### Fastener Installation

{% hint style="warning" %}
#### **Use Of Threadlocker**

Bolts and screws used in the daily use of this aircraft do not require threadlocking compound. This includes the screws holding on the battery trays, rails, and the landing gear parts.

However, for the structural fasteners described in parts of this section blue Loctite 243 compound or equivalent is required. Apply sparingly to the threads before insertion.
{% endhint %}

The Freefly hex drivers included with Alta X Gen2 are designed to limit the torque that can be applied to each bolt or screw and help prevent stripping the fastener head.

Thread all fasteners into their respective holes until snug (when the fastener head bottoms out and lightly clamps the two mating parts together).

To prevent excessive tightening and damaging the fastener or parts, twist the driver from the smaller diameter knurled section of the tool between your thumb and index finger for small fasteners (under size M3) or with your thumb and two forefingers for larger fasteners (size M3 and larger).

**Fastener Torque Values**

Torque Values for Installed Fasteners in Newton-meters (Nm):

<figure><figcaption></figcaption></figure>

Types of bolts:<br>

<figure><figcaption></figcaption></figure>

\
<br>

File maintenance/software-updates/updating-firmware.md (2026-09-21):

# Updating Firmware

## Updating Alta X Gen2 Firmware

{% hint style="info" %}
You can determine if Alta X Gen2 needs an update by following steps 2-4 below. The current firmware version is available on the [Software Updates](./) page.
{% endhint %}

1. Download the firmware from the [Current Firmware Version](./#current-firmware-version) section of the Software Updates page.
2. Connect Alta X Gen2 to your computer with a USB cable.
3. Power on aircraft **with one battery through the fused cable** and wait about 15 seconds for aircraft to fully boot.
4. Using a browser such as Chrome or Safari, open the aircraft's info/update page at [http://10.41.1.1](http://10.41.1.1/) (internet connection is not needed).
5.  In the Update Auterion OS box, click Browse, and select the firmware file downloaded above.

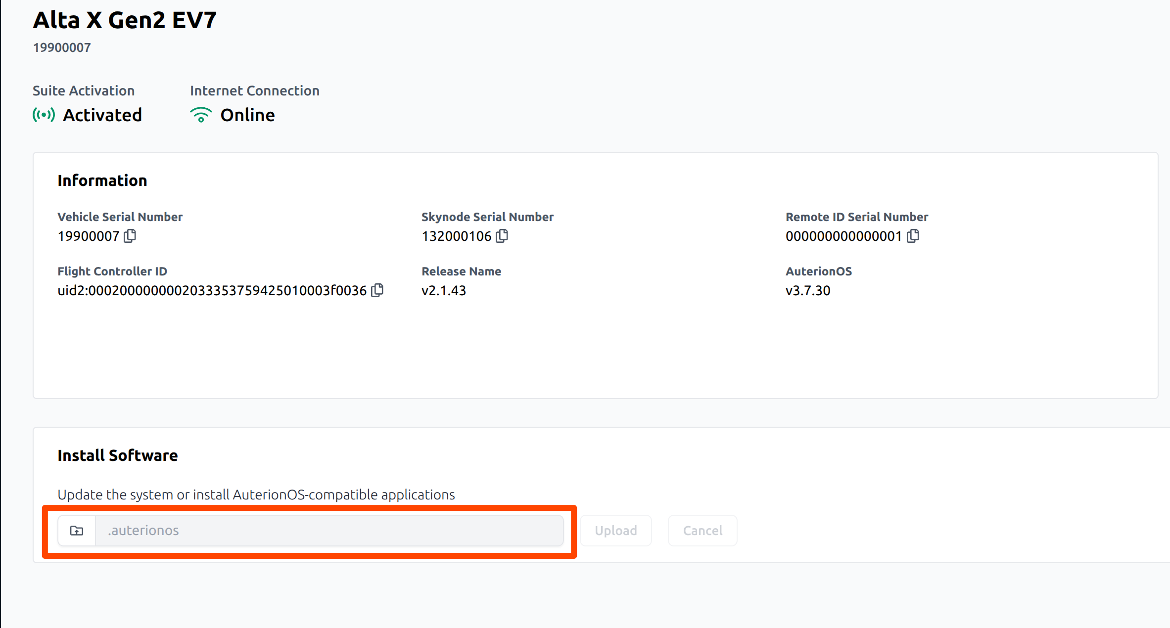
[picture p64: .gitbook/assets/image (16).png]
    <figure><figcaption></figcaption></figure>
6. Click Update and wait 10 mins for the process to complete.
7.  After the update completion message, verify that the webpage shows a "Release name" that matches the downloaded file and that all the boom LEDs are on.

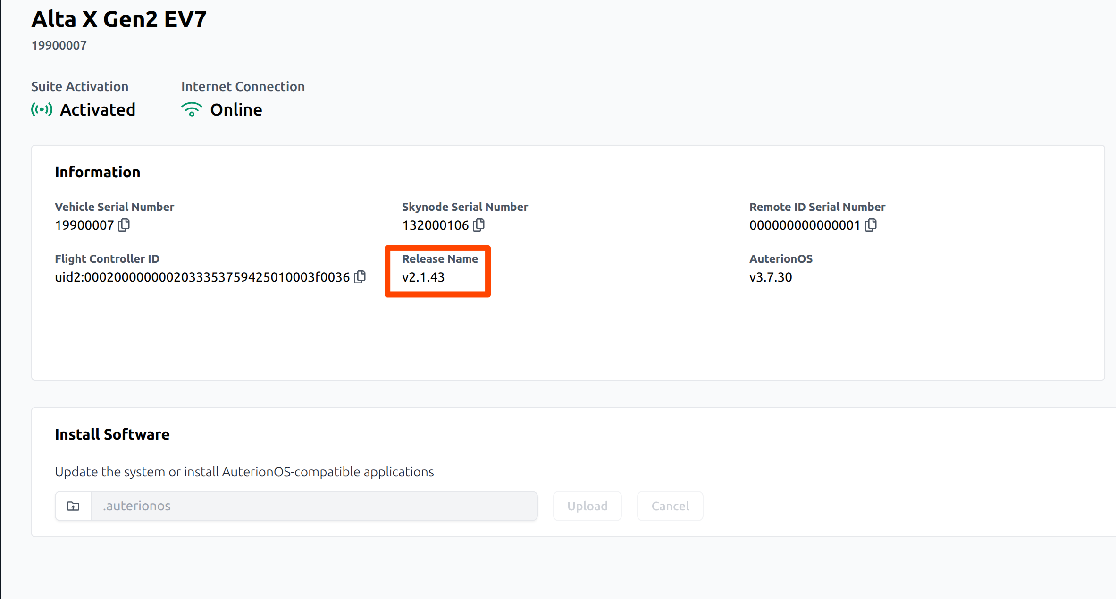
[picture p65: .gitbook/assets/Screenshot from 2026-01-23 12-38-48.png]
    <figure><figcaption></figcaption></figure>

If the aircraft gives an error message, power cycle the aircraft and try again.

{% hint style="warning" %}
**If your Alta X Gen2 firmware update fails:**

1. Update the Pilot Pro App to v2.7 or later.
2. Connect Pilot Pro to your Alta X Gen2.
3. Tap the **Fix Me** button in Pilot Pro, which will apply the _FW Updater Fix_. This is found in:\
   `App Menu > Vehicle Status Page`
4. If you have a Blue/NDAA Alta X Gen2, you will need to disable Admin Protection on the 10.41.1.1/settings page before the _FW Updater Fix_ can apply. Admin Protection can be re-enabled after the firmware update is successful.
5. Retry the Alta X Gen2 firmware update once the _FW Updater Fix_ has been applied.
{% endhint %}

After updating the aircraft, make sure that all apps in the Freefly Updater on Pilot Pro are [up to date](https://docs.freeflysystems.com/ecosystem/controller/pilot-pro/maintenance/software-and-firmware-updates).

***

## How to Reset to Default Alta X Gen2 Parameters

* Open AMC and activate Advanced mode
* Connect AMC to Alta X Gen2
* Select: Vehicle setup > Parameters > Tools > Reset to vehicle's configuration defaults.
* Reboot Vehicle
* Calibrate sensors as required

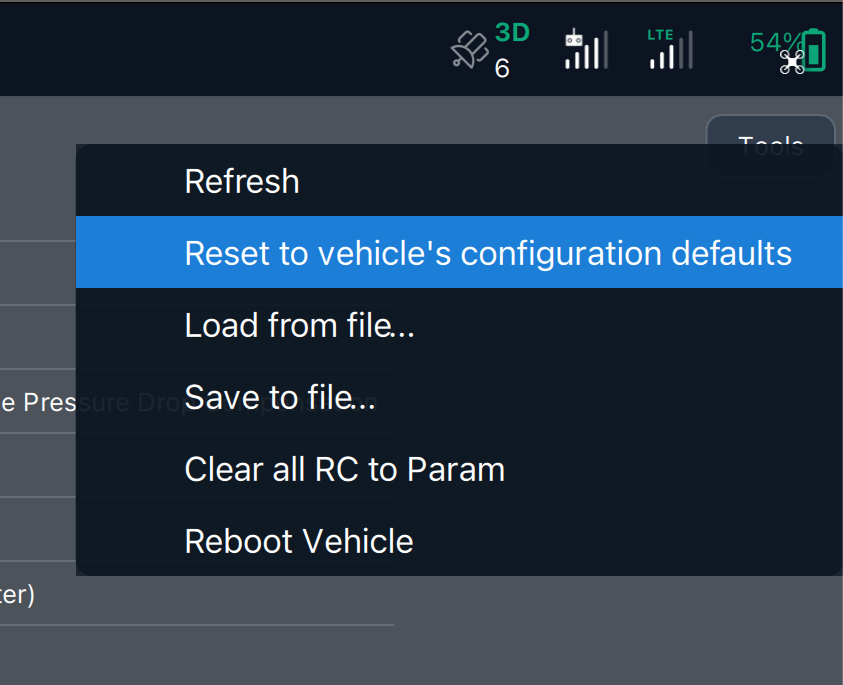
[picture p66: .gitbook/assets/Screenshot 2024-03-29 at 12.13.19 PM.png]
<figure><figcaption></figcaption></figure>

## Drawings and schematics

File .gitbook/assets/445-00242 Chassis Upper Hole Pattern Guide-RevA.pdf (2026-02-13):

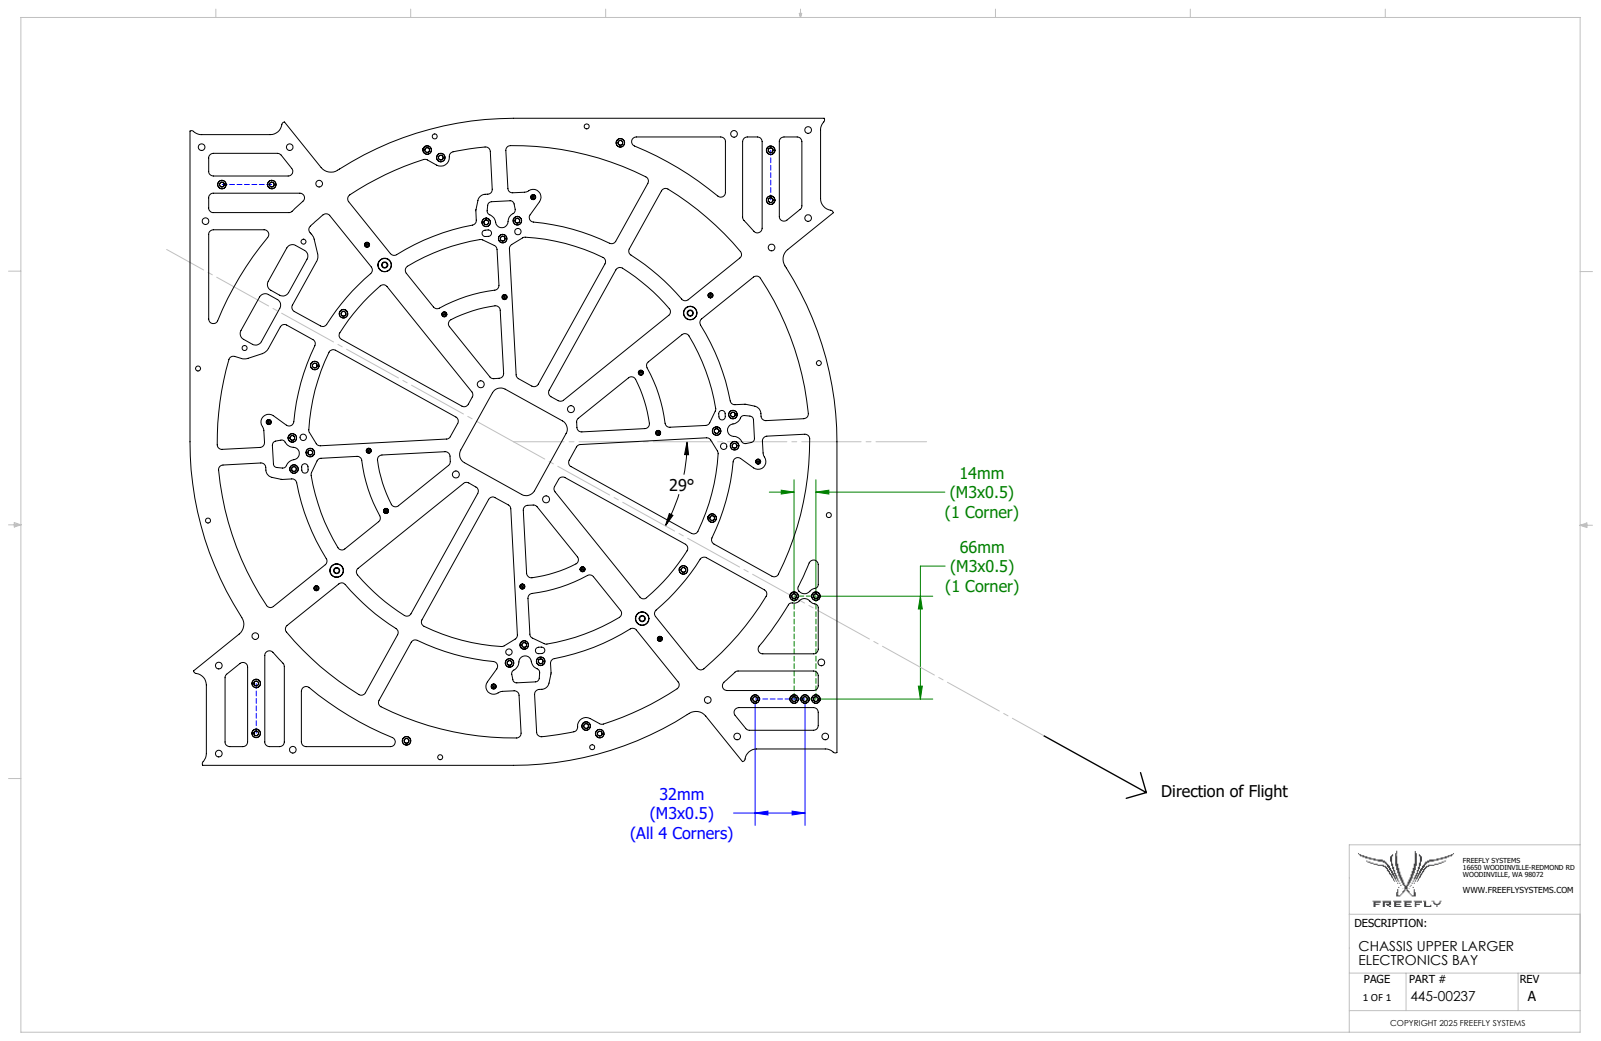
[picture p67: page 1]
(1 Corner); (All 4 Corners); PART #; REV

Direction of Flight

FREEFLY SYSTEMS
16650 WOODINVILLE-REDMOND RD
WOODINVILLE, WA 98072
WWW.FREEFLYSYSTEMS.COM

DESCRIPTION:
CHASSIS UPPER LARGER
ELECTRONICS BAY
PAGE

COPYRIGHT 2025 FREEFLY SYSTEMS

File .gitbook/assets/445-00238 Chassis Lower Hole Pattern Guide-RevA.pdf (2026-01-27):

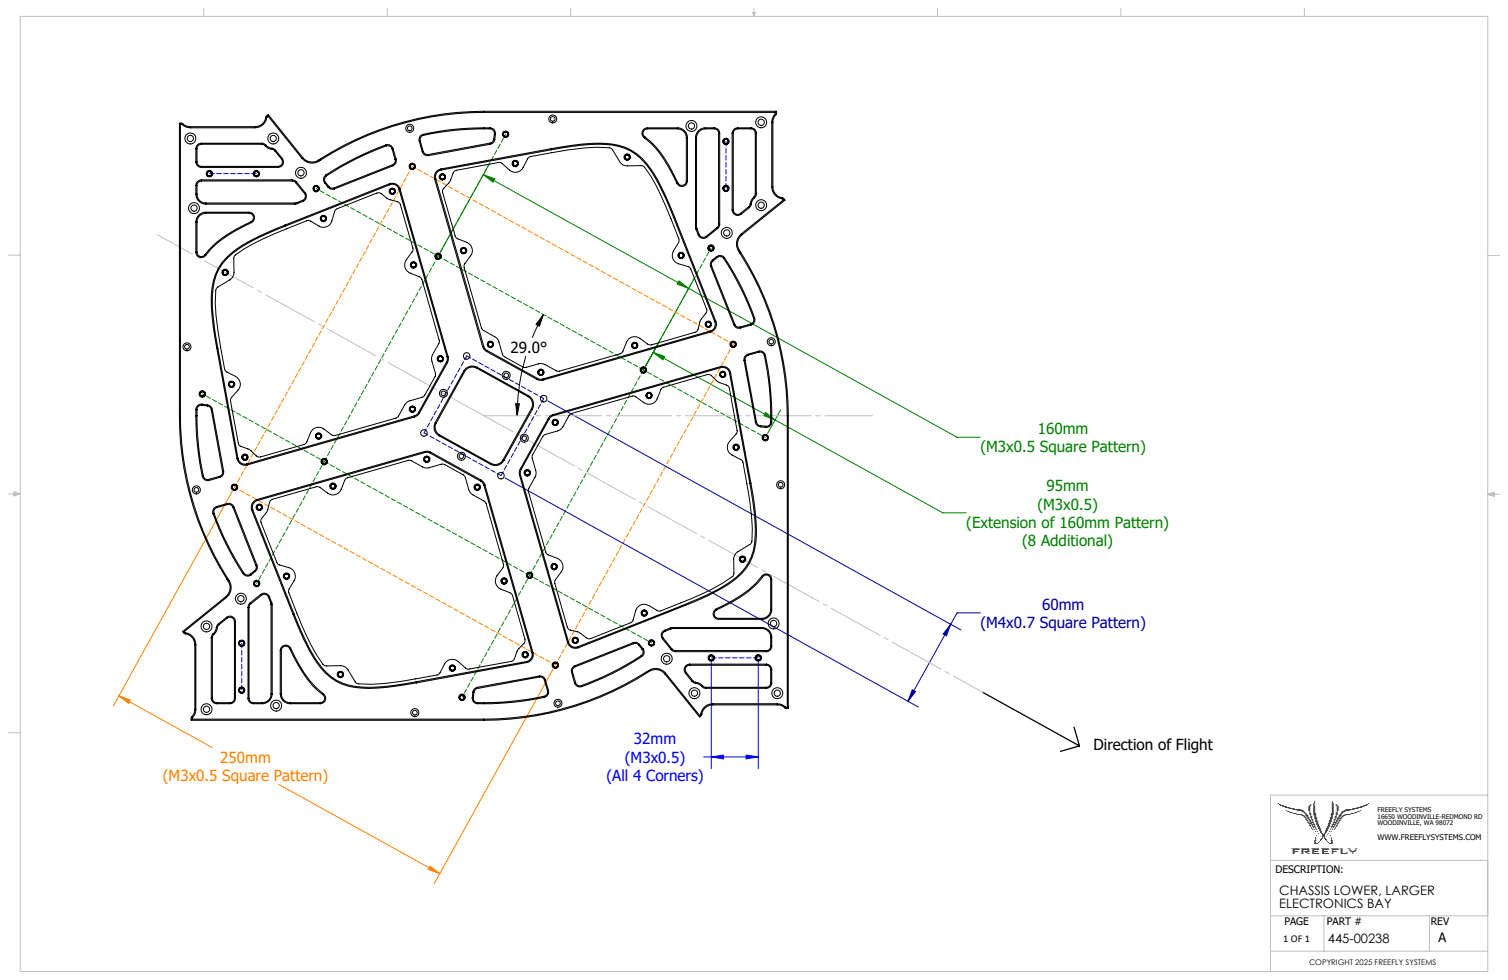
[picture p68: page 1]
(M4x0.7 Square Pattern); (All 4 Corners); (M3x0.5 Square Pattern); (8 Additional); PART #; REV

(Extension of 160mm Pattern)

Direction of Flight

FREEFLY SYSTEMS
16650 WOODINVILLE-REDMOND RD
WOODINVILLE, WA 98072
WWW.FREEFLYSYSTEMS.COM

DESCRIPTION:
CHASSIS LOWER, LARGER
ELECTRONICS BAY
PAGE

COPYRIGHT 2025 FREEFLY SYSTEMS

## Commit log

2026-01-27 GITBOOK-5: No subject
    [430-00494 Mount Compute-Rev01.step, 445-00248 Access Panel Solid-RevA.DXF, 445-00248 Access Panel Solid-RevA.step]
2026-01-27 GITBOOK-6: landing
2026-05-18 Software Updates page and v2.2 release notes
    - split the single Software Updates page into a parent (README) plus an Updating Firmware child, matching Astro's structure
    - preserve the /maintenance/software-updates URL by keeping the folder name aligned with the old page slug
    - add v2.2.6 current release dropdown with firmware download
    - add v2.1.44 as previous release entry
    - add Fix Me / FW Updater Fix warning and Reset to Default Parameters section to the Updating Firmware page
2026-05-18 GITBOOK-13: Added v2.2 Download Button
2026-06-05 GITBOOK-15: Antenna Positioning Images Edited
